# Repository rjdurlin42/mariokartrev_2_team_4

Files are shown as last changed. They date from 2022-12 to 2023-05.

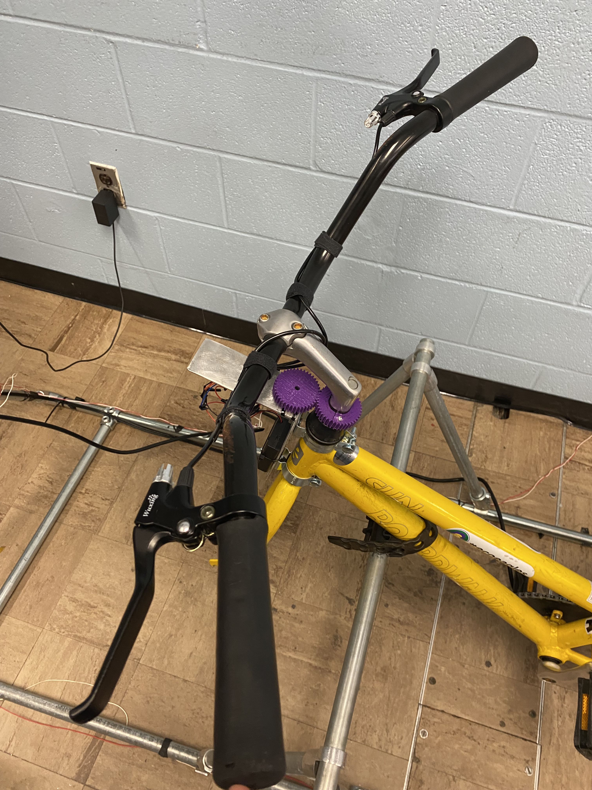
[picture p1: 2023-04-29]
Documentation/Images/Steering Sensor 2.jpg

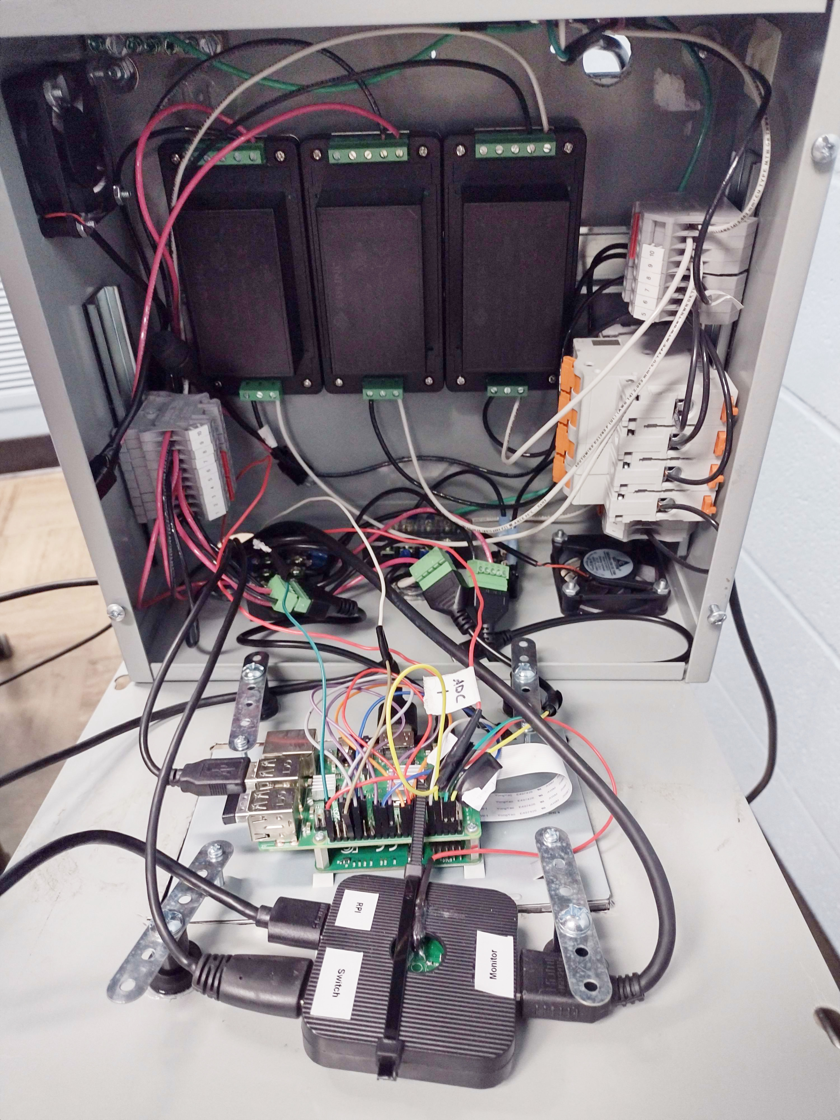
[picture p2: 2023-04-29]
Documentation/Images/Power Subsystem.jpg

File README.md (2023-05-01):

# Mario Kart Bike Version 2

## Executive Summary

The Capstone Design Project Team 4 collaborated to further enhance the riding experience offered by the existing Mario Kart Bike design. Team 4’s design adds a variable of resistance for two modes of operation: the Mario Kart Game Simulation and a Ride Replay Simulation (RRS).  

Improvements to the previous iteration of the Mario Kart Bike offer new dimensions of realism by adding a more dynamic resistance system, while the RRS enables users to record an actual bike ride and then replay it later indoors. Using data gathered from various sensors and an internal physics engine, the RRS processing subsystem calculates whether to speed up or slow down video playback based on the speed the user is pedaling, and it determines the appropriate resistance to apply.

The streamlined resistance system design replaced the cumbersome motor with a linear motor attached to an array of magnets, located perpendicular to a conductive flywheel to generate eddy currents. Opposing magnetic fields generate braking torque in the flywheel, which is transferred to the real bike wheel. This braking torque functions as the resistance felt by the user. The magnetic resistance system utilizes 85 states to create a smooth and realistic replay. The new resistance system also works in the original Mario Kart Bike Mode. 

Team 4 believes the Mario Kart Bike will have a significant impact on the general health of society when the commercialized version is used by Mario Kart enthusiasts and other gamers to participate in physical activity. We also believe our research to achieve a dynamic resistance system can be leveraged for other engineering applications.  

## Capabilities

The Dynamic Resistance System works as designed, providing resistance in the form of braking torque. At a minimum of 411 RPM of the flywheel, the maximum achievable braking torque is 19.432 Nm, and the minimum achievable braking torque is 0.097 Nm. At a maximum of 2,258 RPM of the flywheel, the maximum achievable braking torque is 38.865 Nm, and the minimum achievable braking torque is 0.972 Nm. The bike can be used to play Mario Kart levels, as well as dynamically apply resistance in the Mushroom Cup, via serial commands to the linear actuator. An HDMI switcher button and a play time popup were also implemented. Ride replay data gathering was a success. The Steering Sensor Subsystem is wireless and work as designed. The Speed Sensor Subsystem is hardwired and works as designed. The battery pack power supply for the Steering and Speed Sensor Subsystems is adequate for 2 weeks of run time while in constant use for 4 hours a day. Power distribution and protection comply with the design requirements. 

## Salient Outcomes

##### Dynamic Resistance System
- Resistance felt by the user is applied comparable an exercising spin bike
- Eddy currents are created by moving two magnets closer to a rotating aluminum disk
- Mode of operation: Mario Kart Gaming Simulation 
- Resistance system control
  - PID controller (Arduino Nano, PID_v1 library, maintains 25% duty cycle)
  - MOSFET H-Bridge with discrete components

##### Ride Replay Module (RRSA)
- Data collection (video, elevation, and speed)
- Data storage (removeable 128 GB SD card)
- Data processing (Raspberry Pi Zero W2 specified; Raspberry Pi B2 used due to supply shortage)
- Sensors 
  - Speed (utilizes a magnetic switch (reed switch) and a magnet mounted on bike wheel spoke)
  - Elevation (utilizes a pressure sensor)
- Automatic shutdown on low battery
- Battery life indicator LEDs on power supply

##### Steering and Speed Sensor Subsystems 
- Replaced Speed controller with an Arduino Nano 33 BLE to transfer data by Bluetooth communication
- Added Arduino Nano 33 BLE to the Steering Subsystem to enable the transfer of data by Bluetooth communication
- Designed system to power the Sensor Subsystems using battery packs with 4 lithium AA batteries
- MOSFET was added in the Speed Sensor circuit to save power

##### Steering Sensor Mount Enhancement
- Strengthened and stabilized steering sensor mount 
- Replaced existing plastic 3D printed L-Bracket with metal L-Bracket for enhanced strength
- Attached L-Bracket to bike with conduit hanger for stability 

##### Power Distribution
- Provides device and system protection
- Installation of over protection and Ground Fault Interruption (GFI) protection
- Complete replacement of 120 VAC power supply

## Project Demonstration & Images

Here is the link for the video showcasing the Mario Kart Bike being tested https://youtu.be/U-ZlnsXUXpw.





## About Us

### Team

Team 4 is a 5-person Capstone Design Project Team at Tennessee Technological University, who began Revision 2 of the Mario Kart Simulation Project during the Fall 2022 semester. Team members are Blake Pickett, Ray Durlin, Tyler Chittum, Benjamin Reed, and Sage Mooneyham. All members worked on the Resistance System.
<br />

samooneyha43
##### Sage Mooneyham
- Computer Engineering Major
- Software/Coding
- Bluetooth Communication
<br />

bcpickett42
##### Blake Pickett
- Electrical Engineering Major
- Hardware
- Sensor System
- Steering System
<br />

bdreed43
##### Benjamin Reed
- Computer Engineering Major
- Software/Coding
- HDMI Switching System
<br />

thchittum42
##### Tyler Chittum
- Electrical Engineering Major
- Hardware
- Ride Replay Simulation Acquisition (RRSA) System
<br />

rjdurlin42
##### Ray Durlin
- Electrical Engineering Major
- Hardware
- Power Distribution System

### Faculty Supervisor

The faculty advisor for this project is Jesse Roberts.

### Stakeholders

The main customer for this project is Jesse Roberts, however a commercialized version of this product would likely garner attention from people who enjoy playing Mario Kart, fitness, and/or cycling.

### Recognition

We would like to recognize the work of Reed Hester, Chase Griffin, and Leah Faulkner, the engineers who designed the first iteration of the Mario Kart Bike.

## Repo Organization

### [Reports](https://github.com/rjdurlin42/mariokartrev_2_team_4/tree/main/Reports)

Completed reports can be found in the Reports folder, or by clicking the link above.

### [Documentation](https://github.com/rjdurlin42/mariokartrev_2_team_4/tree/main/Documentation)

Project documentation can be found in the Reports folder, or by clicking the link above.

### [Software](https://github.com/rjdurlin42/mariokartrev_2_team_4/tree/main/Software)

Written software can be found in the Reports folder, or by clicking the link above.

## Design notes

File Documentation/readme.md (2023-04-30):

# Documentation

This folder holds documentation of the project, such as 3D models, wiring schematics, images, and approved signoffs.

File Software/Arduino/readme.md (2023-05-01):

# Arduino Code
This folder holds the code for the steering and speed sensors, as well as the RRS controller. This has both the serial and wireless method of communication with the speed sensor. For the RRS controller, no change is needed to the program for bluetooth as compared to wired serial. Dependencies are found in the include instruction at the top of each file. To run code on sensors, download the files in this folder, install Arduino IDE, install dependencies needed in Arduino IDE, and upload code to individual Nanos via USB. These files are used in conjunction with joycontrol, so you will want to run that as well.

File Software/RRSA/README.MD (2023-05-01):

This folder holds the script used to ride recording functionality in the RRSA subsystem, and the Testing folder contains scripts used to test the functionality of individual aspects of the RRSA. These scripts are designed to be run on the Raspberry Pi platform. In practical implementation, the /etc/rc.local file is configured to run the rrsa.py script on startup.

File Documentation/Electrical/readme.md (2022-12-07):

# Electrical

This folder holds wiring and general electrical schematics.

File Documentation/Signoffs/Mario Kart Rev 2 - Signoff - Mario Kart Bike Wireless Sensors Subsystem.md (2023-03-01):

# Mario Kart Rev 2 - Signoff - Mario Kart Bike Wireless Sensors Subsystem 
## Team 4 - Blake Pickett and Sage Mooneyham ##
<br/><br/>
### _Function of the Subsystem:_ ###

The function of the newly designed feature is to enable Bluetooth LE (BLE) connectivity between sensors and central Raspberry Pi (RPi). These sensors will gather, convert, and send data via BLE (achieved with usage of Arduino Nano 33 BLEs for each sensor) to the master RPi. The wires that rectify and step down the power for the sensors on the current version of the Mario Kart Bike will be replaced with 4 AA batteries and a holder. The 4 AA batteries will provide 6 V and 3500 mAh to the microcontrollers, which will power the sensors for more than 2 weeks.    
<br/><br/>

### _Constraints:_ ###

* **Run Time:**
  * Batteries must supply the DC voltage and current needed to power the equipment for 2 weeks. The equipment shall be able to with stand a minimum of 4 hours of constant use each day during the 2 weeks.     

* **Speed Sensor:** 
  * The KY-032 Obstacle Avoidance Sensor (tachometer) must have a DC voltage between 3.3 V and 5 V, and a minimum of 20 mA to operate correctly. [1]
  * The MIC94053 P-Channel MOSFET must have an input voltage from 1.8 V to 5.5 V. [2] 
  * The MIC94053 P-Channel MOSFET must allow a drain current of 20 mA.  
  * The Nano 33 BLE must have a DC voltage between 5 V and 21 V. [3]
  * The current through the 3.3 pin on the Nano 33 BLE must be less than 100 mA. [4]     

* **Steering Sensor:** 
  * The Potentiometer voltage must be the same as the analog to digital converter (ADS1015).    
  * The ADS1015 must have a DC voltage between 0 V and 5.5 V. [5] 
  * The Nano 33 BLE must have a DC voltage between 5 V and 21 V. [3]
  * The current through the GPIO pins on the Nano 33 BLE must be less than 15 mA. [3]

* **Data Transfer Method:**
  * Communication between the sensors and main RPi must be wireless. Each sensor must have a corresponding Nano 33 BLE in order to achieve BLE communication.

* **Latency:**
  * Communication latency from data sensors to central microcontroller shall be at maximum 40 ms.

<br/><br/>
### _Buildable Schematic:_  ###   

The wiring schematics for the speed and steering sensors are provided in **Figures 1** and **2**.  



**Figure 1.** Wiring Schematic for the Speed Sensor
<br/><br/>



**Figure 2.** Wiring Schematic for the Steering Sensor

<br/><br/>
### _Analysis:_ ### 
<br/><br/>

* **Power Supply for the Speed Sensor:** 
<br/><br/>

  * **_Speed Sensor Batteries:_**
  
      * AA Battery Current = 3500 mAh [6]
      * AA Battery Voltage = 1.5 V [6]
      * Total AA Batteries Voltage = 1.5 * 4 = 6 V
      * Total AA Batteries Wattage = 6 * 3500 = 21000 mWh

  * **_Speed Sensor Current:_**
    
      * Tachometer (running) = 20 mA [1]
      * Tachometer (sleeping)  = 0 mA 
         * The MOSFET is in the cut-off region when Vgs > - Vth. The Vgs = 3.3 – 3.3 = 0  V. The Vth minimum value is - 0.5 V and the maximum value is -1.2 V [2]. Since Vgs = 0 V > Vth = -0.5 V, the drain current Id = 0 A. The tachometer sleeping current is equal to the drain current. 
      * MIC94053 P-Channel MOSFET Current = 0.005 mA [2] 
      * Arduino Nano 33 BLE Default Run Settings = 17 mA [7]  
      * Arduino Nano 33 BLE Sleep Mode (Ram Retention, wake on RTC event) = 0.00316 mA [8]
    <br/><br/>
         * Max current going through 3.3 pin  =  20 mA
         * Current needed (running) = 20 + 17 + 0.005 = 37.005 mA
         * Current needed (Sleeping) = 0 + 0.00316 + 0.005 = 0.00816  mA
         * Total Amp-Hours Needed = (37.005 * 56) + (0.00816  * 280) = 2074.56 mAh    
        
    The speed sensor will use 2075 mAh in 2 weeks of use, which is less than the 3500 mAh that the battery can supply. 
    
    The max current going through the 3.3 pin is 20 mA which is less than 100 mA that the 3.3 pin can with stand. 
    
    The tachometer will be supplied 20 mA when running and 0 mA when sleeping. 
    
    The MIC94053 P-Channel MOSFET will allow a drain current of 20 mA through the MOSFET because the drain current is less than 1.4 amps [2]. The tolerance for the drain current is 1.4 amps [2].
<br/><br/>

  * **_Speed Sensor Voltage:_**
<br/><br/>
    

    **Figure 3.** Discharge of the Ultimate Lithium Energizer AA Battery [6]

    From **Figure 3**, the voltage from of a battery discharging 10 mA or 100 mA drops from 1.5 V to 1.3 V. 

     * Total Voltage Before Discharging =  1.5 * 4 = 6 V 
     * Total Voltage After Discharging =  1.3 * 4 = 5.2 V 

    Therefore, the voltage will stay above the 5 V cutoff voltage of the Arduino Nano 33 BLE even when the batteries have dissipated the full 3500 mAh.

    The input voltage will be regulated by the voltage regulator on the Arduino Nano 33 BLE to 3.3 V. 
    
    The tachometer will be supplied 3.3 V when running and 0 V when sleeping. 
    
    The MIC94053 P-Channel MOSFET will receive 3.3 V for the input voltage which is between 1.8 V and 5.5 V. 
    <br/><br/>

  * **_Speed Sensor Power:_**

    * Tachometer (running) = 20 * 3.3 = 66 mW
    * Tachometer (sleeping) = 0 V * 0 A = 0 mW
    * MIC94053 P-Channel MOSFET Power Dissipation = (Id )^2 * Rds = (20*10^-3)^2 * 76 * 10 ^-3 = 0.0304 mW  
       * Id = tachometer (running) = 20 mA
       * Rds = 76 m ohms [2]
    * Arduino Nano 33 BLE Default Settings = 17 * 6 = 102 mW 
    * Arduino Nano 33 BLE Sleep Mode (Ram Retention, wake on RTC event) = 0.00316* 6 = 0.01896 mW
    <br/><br/>
       - Watts needed (running) = 66 + 102 + 0.0304 = 168.0304 mW  
       - Watts needed (sleeping) =  0 + 0.01896 + 0.0304 = 0.4936 mW
       - Total Watt-Hours Needed = (168.0304  * 56) + (0.4936  * 280) = 9423.5232 mWh  

    The speed sensor will use 9424 mWh in 2 weeks of use. Four AA batteries will provide 21000 mWh, which is sufficient to run the speed sensor equipment for 2 weeks including the 4 hours of constant use each day.
    <br/><br/>

  * **_Speed Sensor Run Time:_**

    Power can be preserved by turning on and off the tachometer (GPIO Pin 22 will be connected to the gate of the MIC94053 P-Channel MOSFET), power LED, and I2C pull-up resistors when needed (done in software) [9][10]. 
    
    A low signal will be asserted to Pin 22 to turn on the tachometer. This will complete voltage connection from the Nano voltage pin (pin 2) to the Tachometer voltage pin( Vcc) allowing current to flow through the tachometer.
    
    A high signal will be asserted to Pin 22 to turn off the tachometer. This will break the voltage connection from the Nano voltage pin (pin 2) to the Tachometer voltage pin( Vcc), creating an open circuit, allowing no current to flow through the tachometer.
    
    This Nano is awoken by event using the RTC timer on the nRF52840 processor. Every 10 seconds (this number is chosen so as to connect in a timely fashion if user wants to activate the controller, while still keeping Nano in sleep a majority of the time), the Nano used for speed data communication will check to see if the central RPi is looking for connection (this means user is attempting to use device). If so, Tachometer is turned back on and actions made before sleeping are reverted. If central RPi is not broadcasting for connection, the Nano will reenter sleep mode (RTC counter).
    
    Dimensions of the battery holders are 2.248 inches (L) by 2.457 inches (w) by 0.622 inches (h). The holders are small/compact to avoid the trip hazard posed by the long wires. Zip ties will securely mount the battery holder to the bike frame. 
    <br/><br/>
    <br/><br/>
    
* **Power Supply for the Steering Sensor:**
    <br/><br/>
    * **_Steering Sensor Batteries:_**

      * AA Battery Current = 3500 mAh [6]
      * AA Battery Voltage = 1.5 V [6]
      * Total AA Batteries Voltage = 1.5 * 4 = 6 V
      * Total AA Batteries Wattage = 6 * 3500 = 21000 mWh

    * **_Steering Sensor Current:_**
    
      * Potentiometer  (running) = 10k ohms [11] = 3.3/10000 = 0.33 mA
      * Potentiometer (sleeping) = 0 / 10000 = 0 mA
      * ADS1015 = 0.3 / 3.3 = 0.09091 mA 
      * Arduino Nano 33 BLE Default Settings = 17 mA [7]    
      * Arduino Nano 33 BLE Sleep Mode (Ram Retention, wake on GPIOTE event) = 0.01737 mA [8]
        <br/><br/>
         - Max current going through IO pins = 0.33 mA
         - Current needed (running) = 0.33 + 0.09091 + 17 = 17.421 mA
         - Current needed (sleeping) = 0 + 0.09091+ 0.01737 = 0.10828 mA
         - Total Amp-Hours Needed = (17.421 * 56) + (0.10828 * 280) = 1981.47 mAh 

      The steering sensor will use 1982 mAh in 2 weeks of use, which is less than the 3500 mAh that the battery can supply.  
      
      The max current going through the GPIO pins is 0.33 mA which is less than 15 mA that the GPIO pins can with stand. 
      <br/><br/>

    * **_Steering Sensor Voltage:_**
    
      From **Figure 3**, the voltage from of a battery discharging 10 mA or 100 mA drops from 1.5 V to 1.3 V.  

         * Total Voltage Before Discharging =  1.5 * 4 = 6 V 
         * Total Voltage After Discharging =  1.3 * 4 = 5.2 V 

      Therefore, the voltage will stay above the 5 V cutoff voltage of the Arduino Nano 33 BLE even when the batteries have dissipated the full 3500 mAh. 

      The input voltage will be regulated by the voltage regulator on the Arduino Nano 33 BLE to 3.3 V.
      
      The GPIO pins will output 3.3 V when given a high signal and 0 V when given a low signal.
      
      The potentiometer and the ADS1015 will be supplied with 3.3 V when their IO pins are given a high signal. Therefore, the voltage on the potentiometer and the ADS1015 will be the same. 
      <br/><br/>

    * **_Steering Sensor Power:_**

        * Potentiometer (running)= 0.33 * 3.3 = 1.089 mW
        * Potentiometer (sleeping) = 0 A * 0 V = 0 mW
        * ADS1015 = 0.3 mW [5]
        * Arduino Nano 33 BLE Default Settings = 17 * 6 = 102 mW 
        * Arduino Nano 33 BLE Sleep Mode (Ram Retention, wake on GPIOTE event) = 0.01737 * 5 = 0.10422 mW
        <br/><br/>
            - Watts needed (running) =  1.089 + 0.3 + 102 = 103.389 mW
            - Watts needed (sleeping) = 0 + 0.3 + 0.10422 = 0.40422 mW
            - Total Watt-Hours Needed = (103.389 * 56) + (0.40422 * 280) = 5902.97 mWh

        The speed sensor will use 5903 mWh in 2 weeks of use. Four AA batteries will provide 21000 mWh, which is sufficient to run the speed sensor equipment for 2 weeks including the 4 hours of constant use each day.
        <br/><br/>

    * **Steering Sensor Run Time:**

      Power can be preserved by turning on and off the potentiometer (Nano GPIO Pin 20), power LED, and I2C pull-up resistors when needed (done in software)[9][10]. 
      
      A high signal will be asserted to pin 20 to turn on the potentiometer. 
      
      A low signal will be asserted to pin 20 to turn on the potentiometer. 
      
      The Arduino Nano 33 BLE will go into sleep mode after the potentiometer, power LED, and I2C pull-up resistors are turned off. Before sleeping, Nano will use the endTransmission Arduino function to end I2C communication. 
      
      The Nano can be woken via a GPIO interrupt event. The GPIO interrupt event that will awaken the switch will be on pin 25 as well as 26 (left and right handlebar button). When the user presses either/both of these, the Nano will wake from sleep, and connect to the central RPi, as well as revert previous actions before it slept.

      Dimensions of the battery holders are 2.248 inches (L) by 2.457 inches (w) by 0.622 inches (h). The holders are small/compact to avoid the trip hazard posed by the long wires. Zip ties will securely mount the battery holder to the bike frame.
      <br/><br/>

 * **Strobing of Receiver:** 

    IR light is emitted from the KY-032 at a frequency of 38 kHz [12], so the receiver (HS0038B) must be cycling at 76 kHz (as a minimum) to satisfy the Nyquist sampling rate. This strobe rate can be programmed manually.  The KY-032 sensor will use the enable pin, which should not be active for more than 2 ms at a time due to the receiver quickly saturating when active [12].

    By determining the time between any two high readings (two markings) and multiplying this time by the number of individual markings, the time required to perform each revolution of the flywheel can be calculated (this calculation will update between every 2 high readings).    

      - (Time between two highs) * (Number of markings) = Time for 1 revolution

    By using the gearing ratio between the flywheel and the bike tire, the current revolutions per second (or minute) at the bike tire can be calculated.    
    <br/><br/>

 * **Bluetooth Connectivity:**

    BLE connectivity for the steering sensor’s microcontroller can use the sensor in conjunction with the ADS 1015 and Potentiometer as well as the left and right handlebar buttons on the bike.    

    Arduino microcontrollers surpass the 5 V limit while others are at 5 V exactly. The Arduino Nano 33 BLE satisfies the power constraint. The Nano 33 BLE measures 45 mm by 18 mm and will within the space constraints of the Mario Kart Bike’s long metal pipes.     
    <br/><br/>

 * **Latency:**

    Latency of communication shall be 40 ms. Network latency can be calculated with the following formula [13]:

      - Latency=(d/v)+(s/r)

    where:

    d = distance of communication in m

    v = speed of transmission medium in m/s

    s = packet size in bits

    r = data transmission rate in Kbps

    In the worst case, the distance equals 2.44 m (central RPi to speed sensor). The transmission speed of Bluetooth LE is 3 * 10^8 m/s (radio waves through air). The maximum transfer unit (MTU) of BLE is 184 bits. Finally, the data transmission rate of the Nano 33 BLE is 270 Kbps. This gives a max transmission latency of 0.68 ms.
    <br/><br/>

 * **Coding:**

    Coding of the Bluetooth modules and their respective microcontrollers can be accomplished in the Arduino IDE, which supports the programming languages C++ and C.  

    Designation of microcontrollers is important, with the sensor’s microcontrollers being peripheral, strictly sending data.  

    The RPi housed in the main component box will be the central microcontroller, or master, primarily receiving data from the peripheral microcontrollers and potentially controlling them if necessary.
    <br/><br/>

  * **Profiles:**

    Bluetooth LE uses a concept of profiles as specification for Bluetooth communication by creating rules that allow certain tasks to be accomplished. The sensors will send bit data to a central RPi, so the Serial Port Profile (SPP) will be used. This profile will define how to set up virtual serial ports and connect two Bluetooth LE enabled devices. 

<br/><br/>
### _BOM:_ ### 

The bill of materials (BOM) to accomplish the design illustrated in the schematics is provided in **Table 1**. 

**Table 1.** Bill of Materials
| Brand / Manufacturer | Part Name | Supplier | Part / Model # or ASIN # | Qty | Units  | Unit Cost | Cost |
| --- | --- | --- | --- | --- | --- | --- | --- |
| LAMPVPATH | 4 AA Battery Holders | Amazon | B07L9M6VZK | 1 | Pack | $7.49 | $7.49  |
| Energizer | 24 Pack AA Lithium Batteries | Amazon | B07BMH7RDP | 1 | Pack | $65.35 | $65.35 |
| Microchip Technology | MIC94053YC6-TR | Digi-key | MIC94053YC6-TR | 1 | Piece  | $0.74 | $0.74  |
| HMROPE | 8 Inch Zip Ties | Amazon | TXLAC | 1 | Pack | $9.18 | $9.18  |
| Duck | Electrical Tape | Amazon | 282289 | 1 | Roll | $1.48 | $1.48  |
| Arduino | Nano 33 BLE | Arduino  | ABX00030 | 2 | Pieces | $26.30 | $52.60 |

<br/><br/>
**References** 

[1]	ArduinoModules, Olawale, I., Ryerson, B., & Chavan, S. (2023, February 15). KY-032 infrared obstacle avoidance sensor module. ArduinoModulesInfo. Retrieved February 24, 2023, from https://arduinomodules.info/ky-032-infrared-obstacle-avoidance-sensor-module/ 

[2] 84mΩ p-channel MOSFET in SC-70-6 - Microchip Technology. (n.d.). Retrieved March 1, 2023, from https://ww1.microchip.com/downloads/en/DeviceDoc/mic94052-53.pdf 

[3] Store.arduino.cc/Nano-33-BLE. (n.d.). Retrieved March 1, 2023, from https://docs.arduino.cc/static/0877c2bf863b3473e961b0b72c8e68ec/ABX00030-full-pinout.pdf 

[4] How to power your arduino? Vin, 5V, and 3.3V pins. How to Power Your Arduino? Vin, 5V, and 3.3V Pins. - Circuit Journal. (n.d.). Retrieved March 1, 2023, from https://circuitjournal.com/arduino-power-pins#:~:text=3.3V%20Pin%20as%20a%20Power%20Output.%20You%20can,can%20supply%20about%20100%20to%20150mA%20of%20current. 

[5] ADS1015. ADS1015 data sheet, product information and support | TI.com. (n.d.). Retrieved March 1, 2023, from https://www.ti.com/product/ADS1015 

[6]	Energizer L91 specifications ultimate lithium. (n.d.). Retrieved February 24, 2023, from https://data.energizer.com/pdfs/l91.pdf 

[7] Team, T. A. (n.d.). Arduino docs: Arduino Documentation. Arduino Docs | Arduino Documentation. Retrieved February 13, 2023, from https://docs.arduino.cc/ 

[8] Arduino. (n.d.). Retrieved February 21, 2023, from https://content.arduino.cc/assets/Nano_BLE_MCU-nRF52840_PS_v1.1.pdf

[9]	How to reduce power consumption on the nano 33 ble. (n.d.). Retrieved February 21, 2023, from https://support.arduino.cc/hc/en-us/articles/4402394378770-How-to-reduce-power-consumption-on-the-Nano-33-BLE 

[10]	Arduino® Nano 33 ble. (n.d.). Retrieved February 21, 2023, from https://docs.arduino.cc/resources/datasheets/ABX00030-datasheet.pdf

[11] Industries, A. (n.d.). Stemma wired potentiometer breakout board - 10K ohm linear. adafruit industries blog RSS. Retrieved March 1, 2023, from https://www.adafruit.com/product/4493#description 

[12]	IR sensor for obstacle avoidance KY-032 (AD-032). IR Senor Obstacle Avoidance Keyes KY 032. (n.d.). Retrieved February 5, 2023, from http://irsensor.wizecode.com/

[13] RF Wireless World. Network Latency Calculator | Network Latency Formula. (n.d.). Retrieved February 13, 2023, from https://www.rfwireless-world.com/calculators/Network-Latency-Calculator.html

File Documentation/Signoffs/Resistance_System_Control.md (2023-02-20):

Team 4 – Mario Kart & Ride Replay Simulator

Team Members: Ray Durlin, Blake Pickett, Tyler Chittum, Benjamin Reed, and Sage Mooneyham

## Detail Design: Resistance System Control Circuit ##

Please note: the scope of this signoff extends only to the control cicuit itself, not to housing components, to the linear actuator, nor to connectors. Also, the signoff document for the resistance system contains BOM listings and information redundant to this document.

### Function of the Subsystem:

- This subsytem acts to control the linear actuator used in the ride resistance system.
- Controls both the direction and speed of the linear actuator.
- Takes an input from the ride replay subsystem over a wireless connection, which determines the distance set point for the linear actuator.
- Takes an input from the linear actuator feedback to determine the current position of the actuator.

### Constraints:

#### Actuator Duty Cycle

The duty cycle of the utilized linear actuator is 25 %. This value must not be exeeded during normal operation. As a result, the controller must be programmable so that the duty cycle may be limited.

#### Actuator Driving Voltage

The utilized actuator is rated for operation at 12 VDC. The control circuit must be capable of providing this voltage to the actuator during operation, so the absolute value of the voltage across the actuator while the system is in either of the two possible on states (foreward and reverse) shall be constrained to 12 V +/- 1 %, assuming the power subsystem provides an input voltage regulated to 12 VDC.

#### Current Capability

The utilized actuator draws a stall current of 7 A, and has a nominal current draw from 1.1 A to 3.4 A. The control circuit must be capable of handling a motor stall without undergoing thermal overload. In addition, the utilized power connector must be capable of handling the total current demand.

#### Wireless Communications

The control ciruit must be capable of recieving a wirelessly-transmitted digital signal from the ride replay system using Bluetooth to update the actuator's position. Since human reaction time is limited to between 100 and 200 ms [1], it follows that the period of data transmission for each packet containing a position value be constrained to be less than 100 ms.

#### Back-EMF Protection

In the course of operation, particularly when the motor is switched off suddenly, a transient voltage potential known as back-EMF will be generated by the motor with opposite polarity to its driving voltage. Due to this, the control circuit shall contain freewheeling diodes to shunt the resulting current away from the switching transistors to prevent damage to the transistors.

#### Mountability

The PCB layout must account for the need to mount the circuit within its housing, as such, screw holes shall be included in the PCB design.

#### Stability

The device must operate without becoming unstable.

#### Resolution

The resistance system has been specified to provide at least 85 unique resistance states, or lengths of linear actuator extension when operating within the specified wheel speed range (from 116 RPM to 288 RPM). To this end, the controller must be capable of monitoring and responding to even the smallest changes in actuator extension correpsponding to a change in resistance state. Please note: from manufacterer correspondance, it is known that it is impossible to guarantee the repeatability of the linear actuator for any controller; furthermore, the actuator to be controlled has already been approved for use. As such, it is impossible to assess the ability of this subsystem to acheive the desired precision from this linear actuator or to select a different linear actuator.

### Schematic and PCB Layout

Schematic

Figure 1: a schematic for the control circuit.

pcb

Figure 2: the PCB layout for the design.

The design files are included within the Electrical subdirectory of the Documentation directory. See links: [schematic](https://github.com/rjdurlin42/mariokartrev_2_team_4/blob/main/Documentation/Electrical/Ride%20Resistance%20System%20Control%20Circuit.png), [pcb](https://github.com/rjdurlin42/mariokartrev_2_team_4/tree/main/Documentation/Electrical/PCB/Sources/Ride%20Resistance%20System%20Control%20Circuit).

### Analysis

#### Actuator Duty Cycle

Arduino PID library contains a function to limit the minimum and maximum PWM duty cycle [2].

Function usage:

     SetOutputLimits(min, max)
     min: the minimum PWM duty cycle
     max: the maximum PWM duty cycle

Where min and max are 8-bit integers, and may be directly-addressed.

The Arduino Nano sets the PWM duty cycle so the maximum PWM cycle may be programatically limited to satisfy the constraint as follows:

     SetOutputLimits(0, 63); //63 is floor[(255)*(25 %)]

Therefore, the constraint is satisfied.

#### Actuator Driving Voltage

     Full load actuator current = 3.4 A @ 12 V
     Linear approximation for motor resistance: Rmotor = 3.529 Ω
     Rds_on(Q1,Q2) = 18 mΩ = 0.018 Ω
     Rds_on(Q3,Q4) = 4.4 mΩ = 0.0044 Ω
     Minimum actuator voltage satisfying constraint = 12 V - 12*0.01 V = 11.88 V

Circuit Analysis:

     On state 1 [Q1 and Q4 on, Q2 and Q3 off]
          |Actuator voltage| = (12 V)*(3.529 Ω)/(3.529 Ω + 0.018 Ω + 0.0044 Ω) = 11.92 V < 11.88 V
     
     On state 2 [Q1 and Q4 off, Q2 and Q3 on]
          |Actuator voltage| = 11.92 V < 11.88 V [by symmetry]

Constraint met.

#### Current Capability

     Linear actuator current at stall = 7 A
     Nominal linear actuator voltage = 12 V
     AMASS XT30 connector current rating = 15 A
     Imax_continuous(Q1,Q2) = 24 A
     Imax_continuous(Q3,Q4) = 45 A
     Stall (worst-case) resistance = (12 V)/(7 A) = 1.714 Ω

By simulation:

     Pd(Q1,Q2) = 1.05 W  < 78 W  = Pmax(Q1,Q2)
     Pd(Q3,Q4) = 0.601 W < 2.5 W = Pmax(Q3,Q4)

Constraint met.

PWM Control Simulation Details:

    Duty Cycle = 25 %
    Switching Frequency = 24 kHz
    Motor Stalled
    Polarity (directional) change at 300 ms
    Switching delay time: 208 to 300 ms
    
spicesim
Figure 3: the LTSPICE schematic prepared for this SPICE simulation.

loadcurrent
Figure 4: the load current. The polarity reverses as expected during the simulation of the directional change starting at 300 microseconds. During the high portions of the PWM cycle, the load current is close to the ideal value of 7 A, meaning the H-bridge produces minimal voltage drop.

Note: It is impossible to fully simulate a motor in SPICE without knowing several mechanical characteristics (moment of inertia, coefficient of viscous friction, and torque) [3] and this information is not given by the actuator manufacturer, so a worst-case non-reactive approximation was used. Back-emf simulation impossible for this reason.

#### Wireless Communications

    Ts < 100 ms = 0.1 s
    Distance resolution: 10 bits (limited by microcontroller ADC)
    Communication protocol: serial
    Communication frequency > 1/(0.1 s) = 10 Hz
    Required samples to update distance variable = (10 bits)/(1 bit/sample) = 10 samples
    Required baud rate > (10 Hz)*(10 samples) = 100 Baud < 9600 = HC-06 default baud rate

Contstraint met.

#### Back-EMF Protection

    Vf(D1,D2,D3,D4) = 0.5 V (approximately)
    Vf(Q1,Q2,Q3,Q4) = 1 V (approximately)
    Rated Peak Current(D1,D2,D3,D4) = 100 A

Specified in datasheet for free-wheeling applications such as this; constraint met.

#### Mountability

Four 2.5 mm diameter screw holes have been included in the PCB design (see fig. 2). These screw holes can accommodate #3 screws. Mounting and housing cutouts to be detailed in motor stand signoff.

#### Stability

Arduino programmable as PID controller [4].

Manufacturer-provided PID constants [5]:

    Kp = 1.80
    Ki = 0.0900
    Kd = 2.50

The above can reasonably be assumed to produce a stable system; therefore, constraint met.

#### Resolution

    Full actuator range = 50.04 mm

Please note: the above value is **not the usable range**, but the full range of the actuator itself; it is stated to clarify the analysis which follows.

    Tmax(max speed) = 121.8499 N•m
    Tmin(max speed) = 0.2712 N•m
    Tmax(min speed) = 28.901 N•m
    Tmin(max speed) = 0.0643 N•m
    See tables 1 and 2 in the resistance system signoff for full specified torque ranges
    Precision of controller: 16 bits
    Unique ADC states across full range = 2^16 = 65536
    ADC full scale range: 0 to 6.144 V
    Feedback voltage range: 0 to 5 V
    ADC States across feedback voltage range: floor[65536*(5 V)/(6.144 V) = 53333]
    Distance precision = (50.04 mm)/(65536) = 0.9382 μm

Using a spreadsheet: (see [Controller_Analysis.xlsx](https://github.com/rjdurlin42/mariokartrev_2_team_4/blob/main/Software/Controller_Analysis.xlsx)):

Equation used:

d_equation

    d:  distance of magnet from flywheel (corresponding to actuator extension lengths)
    Td: developed torque
    ρ:  conductivity
    D:  diameter of magnet
    t:  flywheel thickness
    u0: magnetic permiability of free space
    m:  magnetic dipole moment
    R:  radius of flywheel
    w:  flywheel angular velocity
    Evaluation method: compare the actuation distance required to increment a state at the extrema of the specified 85-state sequences for minimum and maximum speed; compare to determine the smallest distance required to increment a state.
    Result: 10.9 μm
    See EXEL workbook for constant values and formulae
    0.9382 μm < 10.9 μm

Constraint met.

Table 1: miscellaneous component notes and design considerations.
| Component(s) | Design Considerations |
|---|---|
| Switching Transistors (Q1, Q2, Q3, Q4) | Q1 and Q2 only need to switch when the actuator changes direction, and a delay can be programmatically implemented to ensure no current flows during the switching of these transistors. Q3 and Q4 must be able to switch fast enough to handle Pulse Width Modulation (PWM). These FETs have rise and fall times on the order of tens of nanoseconds. As such, they should be capable of handling a PWM signal in the kHz range. |
| Back-EMF Protection Diodes (D1, D2, D3, D4) | Compared to the body diodes of the utilized transistors (Vf ~ 1 V), these diodes provide a forward voltage of equal to or less than 0.5 V, effectively bypassing the transistors during reverse-conduction. |
| Resistors (All) | All resistors in this circuit were subject to only very small power dissipations: less than a milliwatt in all cases. As such, small, common ¼ W resistors were selected. Gate resistors were selected to be surface mount chip-resistors to minimize space usage. The gate driver resistors for the P-Ch FETs are larger than those for the N-Ch FETs, as switching speed is not a priority for the P-Ch FETs. The PWM will be done on the N-Ch FETs, and it is vital that the voltage drop across the gate driver IC be minimized to ensure complete biasing at steady-state.  |
| Pre-Biased Dual NPN IC (U1) | This component is used to bias the gates of the P-Ch FETs, as turning these transistors off will require a voltage of 12 V – a voltage not achievable by using the microcontroller alone. This component was selected because it combines the utility of four resistors and two BJTs into a single package. |
| Arduino Nano (A1) | This microcontroller module was selected because it is already in our stock. It provides an on-board voltage regulator capable of regulating to 3.3 V and to 5 V. The 5 V supply is ideal for providing a logic-voltage reference to the linear actuator feedback and powering the HC-06 module. This microcontroller has a 10-bit DAC on board. |
| Bluetooth Module (MD1) | The HC06 should be capable of providing the required range, as it has a maximum range of about 10 m. In addition to being inexpensive, this module also has the benefit of being very easily connected; it requires only four pins to be connected to the external circuit. |
| Power Connector | The component handles the power input to the circuit, which is then fed into the linear actuator. As such, it must be rated to handle slightly over 7 amperes of current. The AMASS XT30 is rated for 15 A. It also does not allow the user to connect the polarity incorrectly and the mating connector is commonly available in a form that lends itself to the easy fabrication of cables of a custom length without any special equipment. |

### Bill of Materials

Table 2: a BOM for the design. Please note that the Arduino Nano is already in our inventory.

| Level | Part # | Part Name | Supplier |  Supplier Part # | Qty |  Units | Unit Cost | Cost  |
| --- | --- | --- | --- | ---| --- | --- | --- | --- |
| 1 | HBRIDGE100 | Assembly | None | None |  1  |  Assy  | | |
| 1.1 | SOCK100 | AMASS XT30 DC Connector - Male | TME | XT30PW-M |  1  |  Piece | $0.63 |  $0.63  |
| 1.2 | MOSFET100 | G26P04K P-Channel MOSFET | DIGIKEY | 3141-G26P04KCT-ND |  2  |  Piece | $0.78 |  $1.56  |
| 1.3 | MOSFET101 | AOD424 N-Channel MOSFET | DIGIKEY | 785-1565-1-ND |  2  |  Piece | $0.98 |  $1.96  |
| 1.4 | WIFIREC100 | HC-06 Bluetooth Transceiver | ALIEXPRESS  | HC-06 |  1  |  Piece | $2.24 |  $2.24  |
| 1.5 | SOCK200 | Socket Header for Transceiver | DIGIKEY | 2057-SMC-1-04-1-GT-ND  |  1  |  Piece | $0.33 |  $0.33  |
| 1.6 | DIODE100 | B320 Schottky Diode | DIGIKEY | B320-FDICT-ND |  4  |  Piece | $0.48 |  $1.92  |
| 1.7 | BJT100 | DDC114YU-7-F Dual Pre-biased BJT (NPN) | DIGIKEY | DDC114YU-FDICT-ND |  1  |  Piece | $0.43 |  $0.43  |
| 1.8 | CHRESIST100 | CRCW120610K0JNEA 10k Chip Resistor | DIGIKEY | 541-10KECT-ND |  2  |  Piece | $0.10 |  $0.20  |
| 1.9 | CHRESIST101 | ERJ-8GEYJ102V 1k Chip Resistor | DIGIKEY | P1.0KECT-ND |  2  |  Piece | $0.14 |  $0.28  |
| 1.10 |  CARBRESIST100  | CFR-25JB-52-1K 1k THT Resistor | DIGIKEY | 1.0KQBK-ND |  3  |  Piece | $0.10 |  $0.30  |
| 1.11 |  CARBRESIST101  | CFR-25JB-52-2K2 2.2k THT Resistor | DIGIKEY | 	  2.2KQBK-ND |  1  |  Piece | $0.10 |  $0.10  |
| 1.12 | ARDNANO100 | Arduino Nano Microcontroller | Arduino | A000005 |  1  |  Piece | $24.90  |  $24.90 |
| 1.13 | SOCK300 | Socket Header for Arduino | DIGIKEY | 2553-2042-1X15G00SA-ND |  2  |  Piece | $0.74 |  $1.48  |
| 1.14 | ADC100 | ADS1115 4-Channel 16-Bit ADC Module | Protosupplies | MOD-83 |  1  |  Board | $5.95 |  $5.95  |
| 1.15 | SOCK400 | Socket Header for ADC Modele | DIGIKEY | 	ED5864-10-ND |  1  |  Piece | $2.52 |  $2.52  |
| | | | | | | | Total |  $44.80 |

### Citations

[1]R. Whelan, “Effective analysis of Reaction Time Data,” The Psychological Record, vol. 58, no. 3, pp. 475–482, 2008.

[2]B. Beauregard, "SetOutputLimits()," Arduino Playground. [Online]. Available: https://playground.arduino.cc/Code/PIDLibrarySetOutputLimits/. [Accessed: 10-Feb-2023]

[3]"Using SPICE To Model DC Motors," Precision Microdrives. [Online]. Available: https://www.precisionmicrodrives.com/ab-025. [Accessed: 04-Feb-2023].

[4]B. Beauregard, "Arduino PID Library," Arduino Playground. [Online]. Available: https://playground.arduino.cc/Code/PIDLibrary/. [Accessed: 08-Dec-2022]. 

[5]"Pololu - Glideforce GF23-120502-3-65 high-speed LD linear actuator with feedback: 12kgf, 2’ stroke (1.97’ usable), 3.3’/s, 12V," Pololu Robotics &amp; Electronics. [Online]. Available: https://www.pololu.com/product/4951. [Accessed: 08-Dec-2022].

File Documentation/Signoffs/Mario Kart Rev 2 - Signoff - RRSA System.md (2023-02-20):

# Mario Kart Rev 2 - Signoff - Mario Kart Bike RRSA
## Team 4 - Tyler Chittum ##

### Function

The function of the ride data acquisition system is to collect the data necessary to replay rides taken by a rider. The system is required to collect the following: speed, altitude, and video footage. The system records this data and transfers it to the ride replay system by Bluetooth when in proximity.

### Constraints

**C1. Sensor Constraints:** 

The combined inaccuracy of the pressure sensor, the speed sensor, and the resistance system is to be below 10 %.

**C1.1. Pressure Sensor:** The required precision to achieve +/- 1 % accuracy at a granularity of 1 kCal is +/- 4.67 cm. The ride data is to be digitally filtered to attenuate out any ride noise above 1 Hz, so altitude data must be sampled at at least 2 Hz [Nyquist theorem].

**C1.2 Speed Sensor:** The bike wheel speed must be sampled at a frequency of at least 9.6 Hz as the maximum specified bike wheel rotational frequency is 288 RPM, or 4.8 Hz [Nyquist theorem].

**C2. Video Recording:** 

**C2.1. Video Quality:** The resolution is to be 720p with a frame rate of at least 30 fps, and the camera is to be compatible with the Raspberry Pi Zero 2W's camera serial interface. 

**C2.2. Video Data Syncing:** The video footage recorded is to be in sync with the data being measured by sensors.

**C3. Battery life:** The device must be able to continuously operate for at least 3 hours and must provide the user with a visual indication of battery charge status.

**C4. Recording capacity:** The device must be able to capture 3 hours of continuous footage and measurements. 

**C5. Usability:** The device must provide an easily used interface, which is also unobtrusive and does not distract the rider.

**C6. Durability:** The device is to be protected from the outside environment with all electrical components secured to prevent damage while the user is riding.

**C.7 Device Fitment:** The device is to be capable of mounting on any standard mountain bike with no obstructions to the video recording.

### Schematic:

RRSA Schematic
Figure 1: a schematic for the assembly. Not pictured: the camera, which is to be attached to the camera port on the Raspberry Pi Zero 2W.

Overhead View
Figure 2: a drawing illustrating the placement of modules within the project box. The mounting plate is covered in 2.54 mm width square holes. The battery is to be affixed using zip ties. The camera is to be affixed using glue.

Front Panel
Figure 3: the front panel. The mounted components (from left to right): USB-C socket, power switch, start/stop switch.

Camera Hole
Figure 4: the camera hole, which is located on the panel facing away from the rider during use.

Full RRSA
Figure 5: the full assembly with annotations.

Speed Sensor
Figure 6: detail on the speed-sensing portion of the assembly. The reed switch will be secured using two zip ties.

### Analysis:

**A1.1. Pressure Sensor:** 

    Imprecision = 2 cm < 4.67 cm
    Operating range: 300 hPa to 1200 hPa
    Measurement time [high precision] = 105 ms [4]
    Maximum sample rate = 1 ÷ 105 ms = 9.524 Hz > 2 Hz

**A1.2. Speed Sensor:**

    Raspberry Pi GPIO sampling speed = 10 MHz [6] > 9.6 Hz

**A2.1. Video Data Syncing:**

    Raspberry pi time clock rate = 1 MHz
    Time precision = 1 μs
    Max frame desync = 1 μs ÷ (1 ÷ 60 Hz) × 100 % = 0.006 %

**A2.2. Video Quality and Format:**

    Camera recording quality: 720p, 60 fps (or below) [as specified]
    Connection protocol: Rasberry Pi CSI (camera serial interface)
    Formatting capability: MPEG-4 h.264 via ffmpeg

**A4. Recording Capacity:**

    Storage capacity: 128 Gb
    Typical bitrate for as-specified video: 6.5 MB/s [7]
    Video-specific storage = 6.5 MB/s × 60 s/min × 60 min/h × 3 h = 70.2 GB
    Remaining storage = 128 Gb - 70.2 Gb = 57.8 Gb

The remaining storage is the be put to use for sensor data and the operating system.
The SD card used for storage is V10 compliant; rated to record full HD video.

**A3: Battery Life:**

    Raspberry Pi Zero 2W current requirement [stressed] = 580 mA [1]
    Raspberry Pi Camera current requirement [max] = 250 mA [2]
    Raspberry Pi GPIO internal pullup resistor = 33-73 kΩ [3]
    Raspberry Pi logic level = 3.3 V
    Reed switch current draw = 3.3 V / 33 kΩ = 0.1 mA
    DPS310 altitude sensor current draw [max] = 0.345 mA [4]
    Indicator light current draw = 20 mA each [5] = 20 mA × 2 = 40 mA
    Power supply nominal efficiency = 90 %
    Battery energy storage capacity = 24.42 Wh
    Effective battery energy = 24.42 Wh × 90 % = 21.98 Wh
    RRSA power requirement [max] = 5 V × (580 mA + 250 mA + 0.1 mA + 0.345 mA + 40 mA) = 4.352 W
    Projected battery life = 21.98 Wh ÷ 4.352 W = 5.050 hours > 3 hours

Also:

    Recommended constant battery discharge rate = 0.25 C = 1.32 A
    Projected current draw [max] = (4.352 W ÷ 90 %) ÷ 3.7 V = 1.31 A < 1.32 A
    Battery charge rate specification = 1.5 A
    Charge rate limit = 1 A < 1.5 A

**A5. Useability:**

Two button interface; one to turn off and on, the other to start or stop the video recording. The power button has an LED that signifies power on, and the other LED lights when video is being recorded and blinks during data transfer.

**A6. Durability:**

Waterproof box provides protection from weather conditions. Aside from the fasteners shown in figures 2,4,6 [nuts and bolts], glue will be used to seal the entry hole for the speed sensor wires as well as the hole for the camera; zip ties will be used to attach the speed sensing reed switch and the battery.

A7. Device Fitment: The housing attaches to the handlebars using a mechanical twist-locking mechanism and a screw-tensioned ring with rubber adaptors. The bracket requires no tools for removal or installation of the box, and the rubber adapters allow for universal fitment.

**Table 1:** Bill of Materials.
| Subsystem Name: | Ride Data Acquisition System | | | | | | | |
| --- | --- | --- | --- | --- | --- | --- | --- | --- |
| Requested by: | Tyler C. | | | | | | | |
| Approve by: | | | | | | | | |
| Total Cost: | $174.78 | | | | | | | |
| | | | | | | | | |
| | | | | | | | | |
| Level | Part # | Part Name | Supplier | Supplier Part # | Qty | Units  | Unit Cost | Cost |
| 1 | COMP1 | Raspberry Pi Zero 2W | Digikey | 2648-SC0510-ND  | 1 | Module | $15.00 | $15.00  |
| 1.1 | MEM1 | 128 GB Micro SD Card | Newegg | N82E16820215186 | 1 | Module | $10.49 | $10.49  |
| 2 | PSU1 | Power Supply | NONE | NONE | 1 | Assy | | $0.00 |
| 2.1 | MD1 | Adafruit Powerboost 1000 | Adafruit | 2465 | 1 | Module | $19.95 | $19.95  |
| 2.2 | CABLE1 | AK67421-0.3-VM | Digikey | AE11229-ND | 1 | Piece  | $2.58 | $2.58 |
| 2.3 | JACK1 | USB C Jack to USB A Jack Round Panel Mount Adapter | Adafruit | 4259 | 1 | Piece  | $5.95 | $5.95 |  
| 2.4 | CABLE2 | USB cable - 6" A/MicroB | Adafruit | 898 | 1 | Piece  | $2.95 | $2.95 |
| 2.5 | SW1 | Rugged Metal On/Off Switch with Green LED Ring - 16mm Green On/Off | Adafruit | 482 | 1 | Piece  | $4.95 | $4.95 |
| 2.6 | SW3 | Rugged Metal Pushbutton with Red LED Ring - 16mm Red Momentary | Adafruit | 559 | 1 | Piece  | $4.95 | $4.95 |
| 2.7 | BT1 | Lithium Ion Battery Pack - 3.7V 6600mAh | Adafruit | 353 | 1 | Piece  | $24.50 | $24.50  |
| 3 | SENSE1 | Speed Sensor | NONE | NONE | 1 | Assy | | $0.00 |
| 3.1 | SW2 | Hamlin SPST - N.O. High Quality Reed Switch | Electronics Goldmine | G26522 | 1 | Piece  | $2.49 | $2.49 |
| 3.3 | ZT1 | Amazon Basics Multi-Purpose Cable Ties - 4-Inch/100mm, 200-Piece, White | Amazon | DS-SZS-002 | 1 | Piece  | $4.62 | $4.62 |
| 3.4 | MAG1 | Bike Wheel Spoke Computer Magnet | AliExpress | NONE | 1 | Piece  | $1.68 | $1.68 |
| 4 | SENSE2 | Adafruit DPS310 Precision Barometric Pressure / Altitude Sensor | Adafruit | 4494 | 1 | Module | $6.95 | $6.95 |
| 5 | MECH1 | Mechanical Parts | NONE | NONE | 1 | Assy | | $0.00 |
| 5.1 | BOX1 | QILIPSU Clear Hinged Cover 220x170x110mm Junction Box | Amazon | B087F9TS25 | 1 | Piece  | $29.99 | $29.99  |
| 5.2 | MNT1 | Bike Phone Mount, Bicycle Cell Phone Holder with Universal Adapter | Amazon | B08R5K29BC | 1 | Kit | $19.98 | $19.98  |
| 5.3 | FASTENER1 | M2.5-0.45 x 10 mm Zinc Plated Steel Machine Screws (25-Pack) | Home Depot | 311229794 | 1 | 25-Pk  | $6.04 | $6.04 |
| 5.4 | FASTENER2 | M2.5-0.45 Zinc-Plated Metric Hex Nut (5-Piece per Bag) | Home Depot | 204836094 | 3 | 5-Pk | $1.25 | $3.75 |
| 5.5 | FASTENER3 | Gorilla Max Strength Clear Construction Adhesive | Amazon | B0916KZ598 | 1 | Piece  | $7.96 | $7.96 |
| 6 | CAM1 | Camera Module for Raspberry Pi Zero | Pimoroni | CAM003 | 1 | Assy | $10.56 | $10.56  |
| | | | | | | | Total | $174.78 |

### References

[1] L. Pounder, “Raspberry Pi Zero 2 W review: The long awaited sequel,” tomshardware.com, 28-Oct-2021. [Online]. Available: https://www.tomshardware.com/reviews/raspberry-pi-zero-2-w-review. [Accessed: 20-Nov-2022].

[2] jamesh, “Re: Raspberry Pi - camera, reducing power consumption,” Raspberry Pi Forums - Index page, 30-Jul-2011. [Online]. Available: https://forums.raspberrypi.com/viewtopic.php?t=152864. [Accessed: 13-Jan-2023].

[3] A. Scheller, K. Rijnieks, and A. Allan, “Alternative Functions,” Raspberry Pi Documentation. [Online]. Available: https://www.raspberrypi.com/documentation/computers/raspberry-pi.html#alternative-functions. [Accessed: 13-Jan-2023].

[4] “DPS310,” infineon.com, 15-Oct-2020. [Online]. Available: https://www.infineon.com/dgdl/Infineon-DPS310-DataSheet-v01_02-EN.pdf?fileId=5546d462576f34750157750826c42242. [Accessed: 14-Oct-2023].

[5] “Rugged metal on/off switch with Red Led Ring: Technical Details,” adafruit.com. [Online]. Available: https://www.adafruit.com/product/916#technical-details. [Accessed: 13-Jan-2023].

[6] M4H, "Maximum theoretical GPIO sample speed," Raspberry Pi Forums. [Online]. Available: https://forums.raspberrypi.com/viewtopic.php?t=128387. [Accessed: 5-Feb-2023]

[7] “A beginner’s guide to bit rate,” adobe.com. [Online]. Available: https://www.adobe.com/creativecloud/video/discover/bit-rate.html. [Accessed: 22-Nov-2022].

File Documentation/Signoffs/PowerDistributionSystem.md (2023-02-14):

Team 4 – Mario Kart & Ride Replay Simulator

Team Member: Ray Durlin

Detail Design: Main Power Distribution System

<br/><br/>

**Function of the Subsystem:** 

The function of the main power distribution subsystem is to receive an incoming power supply from a 120 Vac, 60 Hz, from a wall receptacle and then 
distribute the power through a protected circuit to multiple devices, which carry varying voltage requirements. The following devices that are to 
receive power from the power distribution subsystem are listed below: 
<br/><br/>
•	5 Vdc

&nbsp;&nbsp;&nbsp;&nbsp; o	Main Controller, MET System (User interface), Fan 1, Fan 2, Arduino 1, and Arduino 2

•	12 Vdc

&nbsp;&nbsp;&nbsp;&nbsp;o	Linear Motor

•	15 Vdc

&nbsp;&nbsp;&nbsp;&nbsp;o	Nintendo Switch

•	120 Vac 

&nbsp;&nbsp;&nbsp;&nbsp;o	Display Monitor

<br/>

The wall receptacle provides power via a ground fault circuit interrupter (GFCI) power cord and then goes through an on/off switch located on the 
distribution enclosure. The power is then routed through a 4-amp circuit breaker. Lastly, the protected 120 Vac power branches to the simulator 
display monitor and three AC/DC power supplies, which feed the 5 Vdc, 12 Vdc, and 15 Vdc devices within the Mario Kart simulation bike. 

The power distribution subsystem is to be enclosed in an aluminum enclosure, which is designed within the power distribution subsystem. The power 
distribution enclosure is to house the user interface screen (HMI), cooling fans, on/off switch, (3) power supplies, and (4) microcontrollers. The 
front panel of the enclosure is to be removable for access and house the HMI display.

<br/><br/><br/><br/>

**Constraints:** 

*Constraints are listed in number for Analysis reference.*
<br/><br/>

*Circuit Design:* 

C1. Each power supply is to be adequately sized to be capable of carrying the maximum power requirement for all the devices within its respective circuit.

C2. All wire sizing is to be in accordance with National Electrical Code Article 210.19(A)(1) based on continuous circuit load [1].

C3. The system will maintain overprotection of the Mario Kart simulator devices with a rating of no less than %125 percent of maximum continuous circuit load as specified by 
the National Electrical Code Article 210.20(A) [1]. 

<br/><br/>

*Safety:* 

C4. All 120 Vac terminals within the user interface are to have been covered and contain a warning of electrocution on the cover. 

C5. Power subsystem must include a means of de-energizing the system via circuit breaker lockout. 

C6. Circuit to include GFCI to ensure that all devices within the Mario Kart simulation are properly protected from ground faults. 

<br/><br/>

*Enclosure:* 

C7.  The enclosure is to be sized to house all devices within the subsystem, excluding incoming and outgoing power cabling.

C8. The front panel containing the HMI is to be removable for access. 

C9. The enclosure is to be fully enclosed and free of any openings. 

C10.  The enclosure is to be properly grounded for protection to protect equipment and possible electrical shock.

<br/><br/>

**Buildable schematic:**



Figure 1. Power Distribution Wiring Diagram

<br/><br/>



Figure 2. Power Distribution Model - Right Side
<br/><br/>



Figure 3. Power Distribution Model - Left Side
<br/><br/>

<br/><br/>

<br/><br/>

**Analysis:**
<br/><br/>
*Analysis is listed in order of constraint reference.*

<br/><br/>

*Circuit Design:*

Devices to be powered within the subsystem below in table 1: 

<br/>

Table 1:

| Circuit Number | Device | Voltage (V) | Voltage Type (AC or DC) | Max Current (A) | Max Power (W) |
|---|---|---|---|---|---|
| 1 | Main Controller | 5 | DC | 3 | 15.00 |
| 1 | MET System (User interface) | 5 | DC | 3 | 15.00 |
| 1 | Fan 1 | 5 | DC | 0.25 | 1.25 |
| 1 | Fan 2 | 5 | DC | 0.25 | 1.25 |
| 2 | Linear Motor | 12 | DC | 3.4 | 40.80 |
| 3 | Nintendo Switch | 15 | DC | 2.10 | 31.50 |
| 4 | Display Monitor | 120 | AC | 0.29 | 35.00 |

<br/><br/>

A1. **Power Supply Sizing:** Based on the power consumption of all devices in table 1, the power supplies are 45 Watts for both the 5 Vdc and 15 Vdc circuits, while the 12 
Vdc circuit power supply is rated for 60 Watts.

Calculation:

120 Vac/5 Vdc Power Supply maximum power = 32.50 W (6.5 A * 5 Vdc)

120 Vac/12 Vdc Power Supply maximum power = 40.80 W (3.4 A * 12 Vdc)

120 Vac/15 Vdc Power Supply maximum power = 31.50 W (2.1 A * 15 Vdc)
<br/><br/>



Figure 4. DC Power Model.
<br/><br/>

A2. **Wire sizing:** The highest rated current devices powered within this subsystem are the linear motor actuator, which has a rating of 3.4 Amps. The design is to use 14 
Gauge THHN stranded rated at 15 Amps, which is at least %125 of the continuous load rating specified in National Electrical Code Article 210.19(A).

A3. **Overprotection rating:** A single 3 Amp circuit breaker is to be upstream of each power supply (manufacturer recommends 3.15 slow blow fuse). Based on the power supply 
circuit protection of 3 Amps each and the maximum current rating of the display monitor, a 15 Amp circuit breaker is to be used to protect the whole system. The 
overprotection device also meets the %125 NEC requirements specified in the National Electrical Code Article 210.20 (A).

Calculation:

(3 A * 3) + 0.29 = 9.29 A

9.74 A * %125 = 11.61 A

<br/><br/>

*Safety Designed:*

A4. **120 Vac Terminals:** All 120 Vac terminals are covered within the enclosure using plexiglass covering with a hazardous warning sticker visible. The hazardous warning is 
to be similar in design to the label represented below in Figure 5. 

<br/><br/>

<br/>
Figure 5. Danger Sign for 120 AC cover.
<br/><br/>

A5. **Means of De-Energizing:** The means of de-energizing the power distrubution subsystem is by removing the power plug from the wall receptable. The power plug is to be 
removed from a wall receptable any time that a power distribution panel is removed.

A6. **Ground Fault Protection:** Additional protection was designed regarding safety using a Ground Fault Circuit Interrupter (GFCI), which is built into the incoming power 
cord of the Mario Kart Simulator. 

<br/><br/>

*Enclosure Design:*

A7. **Enclosure Sizing:** The enclosure is increased from previous design to 12” x 12” x 6” for which to provide a minimum of 2” clearance between all devices and the front 
panel for accessibility. 

A8. **Front Panel Access:** The enclosure includes 4 removeable fasteners to remove the front panel for access. 

A9. **Enclosure Quality:** The enclosure is pre-formed and manufactured by Hammond Manufacturing without any openings and cable clamps are to be used to seal power cable 
input 
and outputs. EPDM rubber is used to create a seal between HMI and inside of front panel.

A10. **Grounding:** Enclosure to be grounded using grounding bar representing in wiring schematic. 

<br/>
<br/>
<br/>
<br/>

**BOM:**
<br/><br/>
| Level | Part # | Part Name | Supplier | Supplier Part # | Qty | Units | Unit Cost | Cost |
|---|---|---|---|---|-----|---|---|---|
| 1 | Enclosure Assembly  | | | | | | | |
| 1.1 | ENCL1 | BOX STEEL GRAY 12"L X 12"W | Digikey | CS12126 | 1 | ea. | $39.65 | $39.65  |
| 1.2 | CBLCLMP-5 | 5-Pack Cable Clamp | Home Depot | 100186543 | 1 | ea. | $4.34 | $4.34 |
| 1.3 | PLXGLS2 | 11 in. x 14 in. x .093 in. Acrylic Sheet | Home Depot | 202090111 | 1 | ea. | $8.28 | $8.28 |
| 1.4 | DINRAIL | TS35 Din Rail 35mm x 7.5mm | DigiKey | ADR3575-U7874-ND | 1 | ea. | $7.06 | $7.06 |
| 1.5 | EPDM | EPDM 1/8 in. x 36 in. x 96 in. Commercial Grade 60A Rubber Sheet | Home Depot | 303371976 | 1 | ea. | $0.00 | $0.00 |
| 2 | Electrical Assembly | | | | | | | |
| 2.1 | PS1 | 120 VAC / 5 VDC Power Supply | DigiKey | 102-PSK-45-5-DIN-ND  | 1 | ea. | $22.65 | $22.65  |
| 2.2 | PS2 | 120 VAC/ 12 VDC Power Supply | Mouser | 490-PSK-60-12-DIN | 1 | ea. | $24.93 | $24.93  |
| 2.3 | PS3 | 120 VAC / 15 VDC Power Supply | DigiKey | 102-PSK-45-15-DIN-ND | 1 | ea. | $22.65 | $22.65  |
| 2.4 | SWTCH | 2 Pos Switch | DigiKey | Z6183-ND | 1 | ea. | $15.89 | $15.89  |
| 2.5 | 14GACONN | 16 - 14 AWG #8 - 10 Stud Size Vinyl-Insulated Spade Terminals, Blue (15-Pack) | Home Depot | 202522889 | 1 | ea. | $3.63 | $3.63 |
| 2.6 | CB-3A | CIRCUIT BREAKER 3A | DigiKey | 277-17752-ND | 3 | ea. | $19.00 | $57.00  |
| 2.7 | 14WIRE | 25 ft. 14 Black Solid CU THHN Wire | Home Depot | 301210609 | 1 | ea. | $0.00 | $0.00 |
| 2.8 | GRDBAR | 4 Terminal Grounding Bar | Home Depot | 100207842 | 1 | ea. | $8.31 | $8.31 |
| 2.9 | GFCI-15 | 15 Amp Compact Right Angle Plug-In GFCI, Black | Home Depot | 205189963 | 1 | ea. | $21.99 | $21.99  |
| 2.10  | WARNLAB | 120 VAC Warning Label | None | None | 1 | ea. | $0.00 | $0.00 |
| 2.11  | TRMBLK | Terminal Block | DigiKey | 277-2026-ND | 10  | ea. | $1.53 | $15.30  |
| 2.12  | TRMJMP | 3 Pos - Terminal Block Jumper | DigiKey | 277-3230-ND | 3 | ea. | $1.80 | $5.40 |
| 2.13  | CONN1 | Linear Motor Control Connector | TME | XT30U-F | 1 | ea. | $0.45 | $0.45 |
| 2.14  | CBMAIN-1 | CIRCUIT BREAKER 15A | Digikey | 277-17761-ND | 1 | ea. | $19.00 | $19.00  |
| 2.15  | TERMSTP4 | 4 Lug Terminal Strip | DigiKey | A98505-ND | 4 | ea. | $2.94 | $11.76  |
| | | | | | | | Total | $288.29 |

<br/><br/>

**References**

[1]    NFPA Link®. [Online]. Available: https://link.nfpa.org/free-access/publications/70/2023. [Accessed: 19-Nov-2022].

<br/><br/>

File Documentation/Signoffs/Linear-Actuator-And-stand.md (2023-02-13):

Team 4 – Mario Kart & Ride Replay Simulator

Team Member: Ray Durlin, Blake Pickett, Tyler Chittum, Benjamin Reed, and Sage Mooneyhamm

Detail Design: Linear Actuator and Stand

<br/><br/>

**Function of the Subsystem:** 
<br/><br/>
The function of the linear actuator stand subsystem is to provide a base for the linear actuator during Mario Kart gameplay and ride replay simulations. The linear actuator 
stand will also house the linear actuator controller. The function of the linear actuator stand is to provide a base for the linear actuator during Mario Kart simulations. 
The linear actuator stand also houses the linear actuator controller. The linear motor’s function is to receive input from the motor control subsystem and provide a feedback 
system to the control.
<br/><br/>

**Constraints:**

<br/><br/>
**Anchoring:** The linear actuator is secured in a manner that the actuator and stand are anchored.

**Grounding:** The case of the linear actuator is to be properly grounded.

**Sizing:** The linear actuator stand is to be sized for the motor controller to be stored inside of the stand.

**Openings:** The linear actuator stand has two openings for the power and control wires from the controller to the actuator. 

**Constructions:** The linear motor stand is to be constructed of materials that will not shield wireless communications of the motor controller. 

<br/><br/>
**Buildable schematic:**

<br/><br/>



<br/>
Figure 1. Right View of 3D model for the Linear Actuator Stand Subsystem
<br/><br/>


<br/>
Figure 2. Rear View of 3D model for the Linear Actuator Stand Subsystem
<br/><br/>


<br/>
Figure 3. Full View of 3D model for the Linear Actuator Stand Subsystem

<br/><br/>
<br/><br/>

**Analysis:**

<br/><br/>

**Anchoring:** The linear actuator is mounted to the stand, which is anchored to the bike stand frame using clamps, and is represented in Figures 1, 2, and 3. The bike 
frame height has a clearance of 10mm, but is also adjustable to endure clamps fits around frame and between the floor.

**Grounding:**  The linear actuator case is grounded to the bike stand frame using 14 Gauge THHN stranded wire, rated for 15 Amps. Paint is to be removed from bike stand 
frame and is represented in Figure 2. 

**Sizing:** The linear actuator stand modeled to be 5.6” x 5.8” x 6.3”, which is capable of containing the controller board that is approximately 3.5” x 2”, while 
maintaining the height required for the resistance subsystem.

**Openings:** Figure 2 shows 2 holes, one circular for power input, and the other a slit opening for the actuator to controller communication/power.

**Constructions:** The linear actuator stand is constructed using 0.5” thick plexi-glass material that will not block communication from the linear actuator controller to 
the main controller.

<br/><br/>
<br/><br/>
**BOM:**
<br/><br/>
The bill of materials (BOM) to accomplish the design illustrated in the schematics is provided in Table 1. 
<br/><br/>
Table 1.

| Level | Part # | Part Name | Supplier | Supplier Part # | Qty | Units | Unit Cost | Cost |
|---|---|---|---|---|-----|---|---|---|
| 1 | LINMOTOR100 | Linear Motor | Pololu | 4953 | 1 | ea. | $183.95 | $183.95 |
| 2 | SCR3 | #3 x 1/2 in. Phillips Head Brass Wood Screw (6-Pack) | Home Dept | 204587520 | 1 | bag | $1.38 | $1.38 |
| 3 | PLXGLS | 20 in. x 32 in. x 0.093 in. Acrylic Sheet | Home Dept | 202038049 | 1 | ea. | $25.48 | $25.48  |
| 4 | CBLCLMP1 | CBL CLAMP P-TYPE BLACK FASTENER | DIGIKEY | N-32B-BK | 2 | ea. | $1.20 | $2.40 |
| 5 | 14WIRE | 25 ft. 14 Black Solid CU THHN Wire | Home Depot | 301210609 | 1 | ea. | $0.00 | $0.00 |
| 6 | 14GACONN | 16 - 14 AWG #8 - 10 Stud Size Vinyl-Insulated Spade Terminals, Blue (15-Pack) | Home Depot | 202522889 | 1 | ea. | $3.63 | $3.63 |
| 7 | SCR2 | #2 x 1/4 in. Phillips Flat Head Zinc Plated Wood Screw (8-Pack) | Home Dept | 204587381 | 4 | bag | $1.38 | $5.52 |
| 8 | LNMTCLP | Routing Clamp | McMaster Carr | 3039T16 | 3 | ea. | $2.92 | $8.76 |
| 9 | BRKPLT | 12 in. x 12 in. 22-Gauge Weldable Sheet | Home Dept | 100237896 | 1 | ea. | $13.57 | $13.57  |
| 10 | AXLMNT | 10mm Universal Aluminum Mounting Hubs for Shaft – 18009 | OzRobitics | 18009 | 1 | ea. | $9.40 | $9.40 |
| | | | | | | | Total | $254.09 |

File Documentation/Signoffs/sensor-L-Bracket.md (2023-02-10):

# Steering L-Bracket Subsystem 
## Team 4 - Blake Pickett ##

_Function of the Subsystem:_

Modifications to the Steering L-Bracket Subsystem will provide stabilized support to ensure that the Gear attached to the Potentiometer meshes with the Gear attached to the handlebars. Both Gears mesh in order for the Mario Kart Bike to perform as designed. The purpose or function of the modifications to the Steering L-Bracket Subsystem is to replace the plastic 3D printed L-Bracket with a metal component and properly attach it to the Mario Kart Bike’s steering column. These revisions will stabilize the Steering Subsystem and increase steering fidelity while creating a form that is more like commercial products.  

_Constraints:_ 

**Increased Fidelity:** The Steering L-Bracket mechanism shall be strengthened using a metal component. 

**Adaptability to Steering Column:** The L-Bracket must be positioned more than 0.25 inches off the steering column. 

_Buildable Schematic:_

**Figures 1**, **2**, and **3** show a 3D model of the Steering L-Bracket Subsystem.



**Figure 1.** 3D Model of Steering L-Bracket



**Figure 2.** 3D Model of Steering L-Bracket



**Figure 3.** 3D Model of Steering L-Bracket

_Analysis:_ 

An analysis has been performed to determine the performance of the existing Steering Subsystem. The results of the analysis and visual inspection indicate that the existing L-Bracket cannot perform as intended. The L-Bracket must be strengthened rather than simply re-placed with a new plastic 3D printed component. The analysis verified that the Steering L-Bracket must be fabricated from metal rather than plastic, and it must be properly secured to the Mario Kart Bike. 

Although analysis indicated that the existing clamps did not break while in use for the previous design, they were not an effective means of attaching/stabilizing the Steering L-Bracket to the steering column because the L-Bracket came in contact with the rubber seal on the Mario Kart Bike’s steering column. Therefore, the clamps must be replaced with conduit hangers to hold the L-Bracket off the surface of the steering column in order to clear the rubber seal.

Specifically, modifications include strengthening the Steering L-Bracket mechanism using a new stainless-steel L-Bracket measuring 12 inches by 7 inches by 2 inches to replace the plastic 3-D printed component. The new metal Steering L-Bracket will be attached to the steering column using two 1-inch conduit hangers. A diagram of the conduit hangers is provided in **Figure 4** [1]. Two holes will be drilled in the L-Bracket, so it can be bolted to the conduit hangers. 

Incorporating a commercially available L-Bracket is a cost-effective solution for providing the necessary strength and stability. Conduit hangers are also commercially available at a minimal cost. 



**Figure 4.** Diagram of Conduit Hanger [1]

_BOM:_

The bill of materials (BOM) to accomplish the design illustrated in the 3D Model is provided in **Table 1**. 

**Table 1.** Bill of Materials
| Brand / Manufacturer | Part Name | Supplier | Part / Model # or ASIN # | Qty | Units  | Unit Cost | Cost |
| --- | --- | --- | --- | --- | --- | --- | --- |
| Ekena Millwork | 12-in x 2-in x 7-in Stainless Steel Support Bracket| Lowe’s | BKTM02X12X07HSCRS | 1 | Pieces | $15.24 | $15.24 |
| Sigma ProConnex | 1-in Steel Conduit Hangers | Lowe’s | 49120 | 2 | Pieces | $0.98 | $1.96  |
| Hillman | 1/4-in- 20 x 1-in Phillips-Drive Machine Screws | Lowe’s | 490435 | 1 | Pack | $1.38 | $1.38  |

**References** 

[1]  _Sigma Proconnex 1-in Schedule 40 schedule 80 zinc-plated steel conduit ..._ (n.d.). Retrieved February 8, 2023, from https://www.lowes.com/pd/Sigma-Electric-ProConnex-1-in-Conduit-Hangers-Schedule-40-PVC-Compatible-Schedule-80-PVC-Compatible-Intermediate-Metal-Conduit-Compatible-Ga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

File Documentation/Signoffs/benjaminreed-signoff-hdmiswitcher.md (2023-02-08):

Team 4 -- Mario Kart & Ride Replay Simulator

Team Members: Ray Durlin, Blake Pickett, Tyler Chittum, Benjamin Reed, and Sage Mooneyham

Detail Design: HDMI Switcher

*Function of the Subsystem:*

The HDMI Switcher is designed to allow users to connect the HDMI ports for their Nintendo Switch and their RRS kit into a single HDMI input to their television or monitor. The switcher that will be used is the BENFEI single-button HDMI switcher (BHS) retrofitted with a Fujitsu NAL-12W-K relay as the switching mechanism. A 1N5818 Diode will protect the This switcher will be installed in the touchscreen compartment and connected to the Raspberry Pi (RPi). If the control bits can be accessed, the Raspberry Pi will interface with a relay to switch between the bits. The button will be replaced by a single pole single throw relay with the switch input originating from a RPi GPIO pin. A 1N5818 diode will protect the RPi from back EMF resulting from the de-energizing of the relay coil [3].

*Constraints:*

*HDMI Compatibility:* The BHS must be rated for 1080p resolutions.

*HDMI Quantity:* The switcher must have at minimum two input HDMI ports and one output HDMI port.

*Relay Voltage/Current Ratings:* The relay coil must be rated for 3.3 V and a maximum 16 mA, and the relay must operate at 3.3 V or below.

*Relay Power Rating:* The power dissipation at the relay coil cannot exceed 70 mW.

*Back EMF Accommodations:* A diode must be implemented in parallel with the relay coil to protect the RPi from back EMF that results from de-energizing the coil [3].

*Background*

As HDMI is standard in the modern era, the multiplexer needs to be compatible with such an input. The RRS Acquisition is designed to record video at a resolution of 720p. Furthermore, the Nintendo Switch is rated to display data at a resolution of 1080p while in TV mode, which is the mode that the Nintendo Switch will be in while using the bike [1].

The Raspberry Pi supplies 3.3 V [2]. A relay with coil terminals rated for these values are necessary. Additionally, to ensure that the relay functions properly, the "must operate voltage" must be less than 3.3 V. Finally, the RPi is limited to a maximum 16 mA output, so the coil drive current must be less than 16 mA to accommodate
 
*Buildable Schematic:*

Screenshot (96)

The schematic shows how the BHS button ports will interact with the relay. However, it is not needed to prove the relay retrofit will work. Relay switches act as a button that completes the circuit when an electrical value is applied to its coil and opens the circuit otherwise. This is identical to how a button works, except the button utilizes the physical depression of the button to complete the circuit. Since these two methods are almost identical in how they connect a circuit, it can easily be inferred that replacing the button with a relay will work.

*Analysis:*

*HDMI Compatability:* The BHS is rated for up to 4K resolutions. This is more than sufficient for the required 1080p resolutions.

*HDMI Quantity:* The BHS is designed as a two-to-one HDMI switcher. This satisfies the two-port constraint.
*Relay Voltage/Current Rating:* The TXS2-L-3V is rated with a must operate voltage of 2.4 V and a maximum voltage of 4.5 V [4]. In addition, the relay current is 11.7 mA, which is rated within the operating range of the RPi.

*Relay Power Rating:* The equation for power is P = I^2^R. In this case, the power is calculated as

P = 0.0117A^2 (257 Ω)

P = 35 mW

Therefore, the relay must be rated for 35 mW. The TXS2-L-3V relay is rated for 70 mW and is therefore sufficient [4]. Additionally, for the 3.3V pulse, the equation is

P = V^2/R

P = 3.3V^2/257 Ω

P = 43 mW

 which also shows the relay rating is sufficient.

*BOM*

| Team 4 - Mario Kart & RRS | Bill of Materials (BOM) | | | | | | | |
| --- | --- | --- | - | - | - | - | - | - |
| Subsystem Name: | HDMI Switcher | |  |  |  |
| Requested by: | Benjamin R | |  |  |  |
| Approve by: | | |  |  |  |
| Total Cost: | $16.69 | |  |  |  |
| | | |  |  |  |  |  |  |
| | | |  |  |  |  |  |  |
| Level | Part # | Part Name | Supplier | Supplier Part # | Qty | Units | Unit Cost | Cost |
| 1 | BHS100 | HDMI Switcher | BENFEI | N/A | 1 | Emb. System | $10.99 | $10.99 |
| 2.1 | RELAY100 | TXS2-L-3V Relay | Digikey | 255-1899-ND | 1 | Piece | $5.30 | $5.30 |
| 2.2 | DIODE100 | 1N5818 Diode | Digikey | 497-4548-1-ND | 1 | Piece | $0.40 | $0.40 |
| | | |  |  |  |  | Total | $16.69 |

REFERENCES

[1] Nintendo, "Technical Specs." nintendo.com. https://www.nintendo.com/switch/techspecs/#switch-section (accessed Nov. 21, 2022).

[2] Raspberry Pi Ltd., "Raspberry Pi 4 Model B." raspberrypi.com. https://datasheets.raspberrypi.com/rpi4/raspberry-pi-4-datasheet.pdf (accessed Nov. 21, 2022)

[3] Durakool, “A Layman’s Guide to Coil Suppression.” Durakoolrelays.com. https://www.durakoolrelays.com/information/technology/layman-s-guide-to-coil-suppression/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,Back%20EMF%20(Electromotive%20Force).

[4] Panasonic, “TX-S Relays.” Panasonic.eu. https://mediap.industry.panasonic.eu/assets/download-files/import/mech_eng_txs.pdf

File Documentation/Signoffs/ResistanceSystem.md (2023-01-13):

Team 4 – Mario Kart & Ride Replay Simulator

Team Members: Ray Durlin, Blake Pickett, Tyler Chittum, Benjamin Reed, and Sage Mooneyham

## Detail Design: Resistance System ##

### Function of the Subsystem:

The function of the resistance system is to control and vary the resistance felt by the user of the Mario Kart Bike, hereafter referred to as the bike.  

- The controller monitors the linear actuator feedback voltage to determine its current position with 10-bit precision, which corresponds to the distance of the magnet array from the flywheel. 

- An external digital input (via the Bluetooth module) is received from the ride replay subsystem to determine the calculated set point which the actuator should extend to. This recieved value corresponds to a resistance state, of which there are 511; the limiting factors being the 10-bit precision of the controller and the usable portion of the actuator's range.

- The controller supplies either a positive or negative voltage to the linear actuator to control the direction of the actuator's motion.

- The actuator is to vary the array of magnets perpendicular to the simulator’s rear conductive flywheel (not the current flywheel on the bike, a new flywheel with dimensions that fit our design more effectively) to generate eddy currents using the primary magnetic induction formed at the conductor [1], which result in the generation of braking torque opposed onto the flywheel. 

- The braking torque will transfer from the flywheel to the rear bike tire, and then from the rear bike tire to the rider’s pedals, which will act to resist the pedaling of the rider. 

### Constraints:

#### Magnet Distance Range: 

- A distance range of 2-25mm from magnet to flywheel was selected, as these distances matched up well with the torque values that we want the resistance system to apply. 

#### Minimum Tire Speed: 

- The minimum speed of the bike tire shall be considered 116.35 rpm. This value is based on the American Council on Exercise's recommendation for the minimum speed required for moderate exercise on a bike [2]. This correlates to 2501.52 rpm in the flywheel (conversion is explained in later sections). At speeds less than 116.35 rpm, the torque placed on the rider will not be specified to reach any minimum value, and the resulution of the resistance changes within this operating region is not specified.

#### Maximum Tire Speed: 

- The maximum speed of the bike tire shall be considered 288 rpm, a value that comes from the average pedaling rpm (118 rpm) of an elite level cyclist [3] (Wheel to pedal gear ratio = 2.444, so wheel speed = 2.444*pedal speed). This correlates to 6192 rpm in the flywheel due to the the rotational velocity ratio of 43:2 between the flywheel and the wheel. If the user passes this speed, no additional torque will be applied to avoid injury to rider. 

#### Maximum Torque at Minimum Speed: 

- Using the value for tire minimum speed (116.35 rpm), we know that the maximum torque at this speed will be produced when the magnets are closest (2mm). From here, you can find magnetic field felt at the flywheel using equation 2. These values can be plugged into equation 1 to give the torque at the flywheel, which can then be converted to torque at the bike wheel/pedals using the gearing ratios between the components (this is explained in more detail later in the document). Using this logic, we find that the max torque at the minimum speed is 49.23 Nm. 

#### Minimum Torque at Minimum Speed: 

- Using the above logic while setting magnet distance to the furthest value (20mm) and wheel speed to the minimum value, we find the minimum torque at minimum speed is 0.002 Nm. 

#### Maximum Torque at Maximum Speed: 

- Using the above logic while setting magnet distance to the closest value and wheel speed to the maximum value (288 rpm), we find the maximum torque at maximum speed is 121.85 Nm. Safety always being a concern, this force is much lower than what is needed to break any leg bone in the average person. [4] [6]. 

#### Minimum Torque at Maximum Speed: 

- Using the above logic while setting magnet distance to the furthest value and wheel speed to the maximum value, we find the minimum torque at maximum speed is 0.004 N•m. 

#### Resistance Resolution: 

- The resistance system will have a resolution of at least 85 states. 

- The controller will allow for 10-bit resolution or 1024 unique states. 

The linear actuator used has a length of 1.97". In practical usage, we would use 45.97 % of this range, yielding an effective number of states of 470.

Note: The minimum and maximum speeds referenced within this section have been converted to bike tire rpm, so the units of measure are consistent throughout the report. The pedaling speed sourced from the reference was multiplied by the gear ratio from the front to rear sprocket, which was 2.44. The speed of the bike is referred to in the units of bike tire revolutions per minute (rpm). 

### Buildable Schematic:



Figure 1. Resistance System Full View



Figure 2. Close Up of Linear Actuator, Flywheel, Magnet Holder



Figure 3. Close Up of Linear Actuator, Flywheel, Magnet Holder with Different Viewpoint

### Aluminum Flywheel:

•	An aluminum circle with a radius of 101.6 mm (4”) will be cut from a sheet of aluminum material. 

•	A hole will be drilled in the center of the aluminum flywheel. 

•	The steel flywheel on the UNISKY bike stand will be replaced with the new aluminum flywheel. 

&ensp;&thinsp; &ensp;&thinsp; •The bolt holding the steel flywheel will be unscrewed.
   
&ensp;&thinsp; &ensp;&thinsp; •The steel flywheel will be replaced with the aluminum flywheel.
   
&ensp;&thinsp; &ensp;&thinsp; •The bolt will be screwed back into place on the bike stand.
   
•	The drive wheel at the back of the UNISKY bike stand will be screwed into the rear wheel of the bike.

&ensp;&thinsp; &ensp;&thinsp; •	This will ensure maximum transfer of energy when the magnetic breaking occurs to the flywheel. 
   
•	The UNISKY bike stand will come with a magnetic brake which will be removed. 

*Bracket:*

•	For the magnetic portion of the resistance system, two mounting brackets will be welded to a metal block stand.

&ensp;&thinsp; &ensp;&thinsp; • The two mounting brackets will be separated by 246 mm to allow for proper mounting of the linear actuator. 

•	The linear actuator will be hooked to the two mounting brackets. 

•	A 14 mm square bracket will be welded to the circular steel bracket.

•	Two magnets will be attached to the opposite side of the circular bracket using the ferromagnetic properties of the steel to hold the magnets in place.

•	The linear actuator will be attached to the square bracket. 

### Analysis:

#### Method of Data Analysis for Calculating Torque: 
The resistance system is centered on the electromagnetic topic of eddy currents and Lenz’s Law. An equation found in a publication for the Centre for Intelligent Machines that models the function of an eddy current braking system was utilized to determine the attributes of the resistance system components [1]. Specifically, the torque achieved depends on angular speed, as well as magnet distance from the flywheel. The function is shown below. 

 
</br> where, 

σ = Conductivity of flywheel material  (Ω−1m−1) </br>
D=magnet diameter (meters) </br>
d = disc (flywheel) thickness (meters) </br>
B = magnet field strength (Tesla) </br>
R = dist from flywheel center to magnet (m) </br> 
θ = angular velocity (rads/s) </br>

This equation was used to determine the torque produced in the flywheel at varying magnet distances and angular speeds. This torque can then be used to find the torque felt in the bike tire, as well as pedals, by applying the flywheel to tire gear ratio (43:2) or tire to pedal gear ratio (43:18), respectively. The following values were determined from the onset. 

- The bicycle’s wheel radius is a known constant of 0.33 m.  

- The flywheel’s radius is a known constant of 0.1016 m. 

- The flywheel’s thickness is a known constant of 0.0127 m. 

- The magnet’s diameter is a known constant of 0.0508 m. 

- The material for the flywheel is aluminum because aluminum has the highest conductivity for the cost, allowing the resistance system to reach the necessary torque values. Therefore, this value is 3.77*107 (Ωm)-1. 

- The axis-to-pole value was set to be approximately 0.305 m. This distance was determined by the flywheel’s radius minus the maximum radius of the magnet options available. Torque is maximized when the magnets are at the edge of the flywheel. 

#### Method of Data Analysis for Calculating Distance between Magnet and Flywheel (Air Gap):

The magnetic field and angular speed can be considered the varying components in torque calculation.  The angular speed will determine the magnet distance (field strength at the flywheel) needed to produce certain torque states. The resistance system will vary the distance between 2 mm and 25 mm. 

The linear motor will increase or decrease the distance from the aluminum flywheel to the magnet (air gap), resulting in an increase or decrease in the magnetic field the flywheel experiences. The distance to magnetic field relationship can be modeled using Equation 2 below, which was found within the magnet suppliers’ website [5].



where,

μ_o=magnetic permeability in a vaccum (Tm/A)

m = magnetic moment (Am^2 )

r=dist. from magnet to flywheel (m)

Because the x-component of the point of measurement on the flywheel is zero, the total magnetic field at the flywheel is equal to the y-component of the magnetic field. 

Magnetic moment of the magnet can be found using Equation 3 found within the magnet suppliers’ website [5].



where, 

B_(r )= residual field (Gauss)

V = magnet volume (m^3 )

The disk magnets utilized in the analysis are 2 inches in diameter and 0.125 inches in thickness. The supplier part number for K & J Magnetics is DY04-N52 [5]. The magnet used in the analysis was determined based on the supplier’s documented shape and field strength. The optimal shape of the magnet for this analysis is a disk shape. The disk shape allowed the team to apply Lenz’s formula without further adaptation. The DY04-N52 magnets have a surface field of 1795 Gauss, which is the ideal field strength to the torque generated by the eddy currents within the resistance system based on the analysis gathered within this report.

*DY04-N52 Magnet Characteristics:*

•	Residual field provided by the magnet suppliers is14,800 Gauss

•	Volume is calculated to be 1.287E-5 m^3

•	Calculated magnetic moment of 15.158 Am^2 

Note: The calculated distance between the magnets and the flywheel required to control the resistance felt by the user will be calculated by the Ride Simulation System (RSS) processing subsystem and is an external input to the resistance subsystem.

#### Minimum Speed Analysis: 

Objective: To prove that the resistance system can provide and vary torque while the rider is traveling at a minimum speed of 116.35 rpm.  

The plots in Figures 6 and 7 are a representation of provided torque, based on the magnetic field between the magnet and flywheel using Equation 1. 



Figure 4. Torque on Rider at Minimum Speed.



Figure 5. Torque Generated at Flywheel at Minimum Speed.

The analysis validates that the resistance system can provide and vary torque braking torque while operating at the minimum speed of 116.35 rpm, with a distance range of 2-25mm between magnet and flywheel. For the minimum speed analysis, the flywheel speed was calculated at 2501.6. To calculate the flywheel speed, the bike tire rpm was multiplied by 21.5. The value of 21.5 is the gear ratio between the bike tire and the flywheel.  

#### Maximum Speed/Maximum Torque Analysis:

Objective: To prove that the resistance system can provide and vary torque while the rider is traveling at a maximum speed of 288 rpm.



Figure 6. Torque on Rider at Maximum Speed.



Figure 7. Torque Generated at Flywheel at Maximum Speed.

Figures 8 and 9 show the torque generated by the resistance system while the rider is at the maximum speed of 288 rpm. The maximum torque that the resistance system can generate will occur at the maximum speed of the bike, with the closest distance between magnet and flywheel. We can see in Figure 8 that the maximum achieved torque is equal to 121.845 Nm. The increased torque generated is the result of an increase in eddy currents, which is represented in Equation 1 in the form of angular velocity (Rad/s). Analysis validates that the maximum torque that the resistance will provide to the rider is 121.845 N•m 

#### Resistance Resolution Analysis:

•	The torque values were calculated by determining incline angle, denoted α, increases that resulted in 10 % increases – give or take 3-4 % – in resistance, given by sin(α), for a range of 0° to 40°. This was done in accordance with the previous specifications proposed for this project.

•	The torque values were determined by scaling the resistance values by that of the 85th state, then multiplying all values by 28.9 Nm to find fractions of our maximum torque.

•	This process was completed using a MATLAB script, which are in the project folder under the name state_test.m. The torque values, in Nm, are shown in Table 1. 

#### Torque Values in Nm at Minimum Speed

| Table 1. | | | | | | | | |
|---|---|---|---|---|---|---|---|---|
| 0.0643 | 0.0693 | 0.0742 | 0.0841 | 0.0940 | 0.1039 | 0.1138 | 0.1237 | 0.1336 |
| 0.1435 | 0.1583 | 0.1732 | 0.1880 | 0.2029 | 0.2177 | 0.2375 | 0.2573 | 0.2771 |
| 0.2969 | 0.3216 | 0.3463 | 0.3711 | 0.4008 | 0.4305 | 0.4651 | 0.4997 | 0.5393 |
| 0.5789 | 0.6234 | 0.6679 | 0.7174 | 0.7718 | 0.8262 | 0.8856 | 0.9499 | 1.0192 |
| 1.0934 | 1.1725 | 1.2566 | 1.3456 | 1.4445 | 1.5484 | 1.6572 | 1.7759 | 1.9044 |
| 2.0379 | 2.1813 | 2.3345 | 2.5025 | 2.6804 | 2.8681 | 3.0706 | 3.2879 | 3.5198 |
| 3.7666 | 4.0329 | 4.3189 | 4.6244 | 4.9494 | 5.2988 | 5.6725 | 6.0704 | 6.4974 |
| 6.9533 | 7.4428 | 7.9657 | 8.5268 | 9.1256 | 9.7667 | 10.454 | 11.188 | 11.972 |
| 12.811 | 13.712 | 14.674 | 15.705 | 16.808 | 17.989 | 19.249 | 20.599 | 22.041 |
| 23.586 | 25.239 | 27.007 | 28.901 | | | | | |

In order to find the minimum change in torque required for the design, the values of torque up to the maximum torque attainable at the minimum speed was calculated via the prior algorithm. The smallest change in torque present within the resulting list was 0.0084 N•m, which corresponds to the very first two states in the list. The difference in torque corresponding to the difference in distance between the furthest two possible positions which the controller can set the actuator in a range extending from 2 mm to 25 mm is 0.141 micro N•m.

#### Torque Values in Nm at Maxium Speed

| 0.2712 | 0.292 | 0.3129 | 0.3546  | 0.3963  | | |
|---|---|---|---|---|---|---|
| 0.4381 | 0.4798 | 0.5215 | 0.5632  | 0.6049  | 0.6675  | 0.7301  |
| 0.7927 | 0.8553 | 0.9179 | 1.0013  | 1.0847  | 1.1682  | 1.2516  |
| 1.3559 | 1.4602 | 1.5645 | 1.6897  | 1.8148  | 1.9608  | 2.1069  |
| 2.2737 | 2.4406 | 2.6283 | 2.8161  | 3.0246  | 3.2541  | 3.4835  |
| 3.7338 | 4.0049 | 4.2969 | 4.6098  | 4.9434  | 5.2979  | 5.6733  |
| 6.0903 | 6.5282 | 6.9869 | 7.4872  | 8.0292  | 8.592 | 9.1964  |
| 9.8424 | 10.5508  | 11.3007  | 12.0922 | 12.9459 | 13.8619 | 14.84 |
| 15.8802  | 17.0031  | 18.2087  | 19.4967 | 20.8671 | 22.3402 | 23.9158 |
| 25.5935  | 27.3937  | 29.3157  | 31.3795 | 33.5843 | 35.9497 | 38.4743 |
| 41.1772  | 44.0768  | 47.1708  | 50.4765 | 54.0107 | 57.809  | 61.8656 |
| 66.2133  | 70.8628  | 75.8423  | 81.157  | 86.8467 | 92.9265 | 99.4416 |
| 106.4082 | 113.8654 | 121.8499 | | | | 

Table 2

The table above showcases 85 states of resistance, utilizing a variance of magnet distance to flywheel. From these two tables, we can see that at least 85 states of resistance can be created at any speed, simply due to the linear actuator being able to provide 85 different magnet distances, regardless of speed.
</br>
</br>

*Control Circuit Components Analysis:*

An analysis of selected control circuit components and the resultant relevant design considerations are provided in Table 3.

| Table 3: Analysis of Selected Control Circuit Components and Design Considerations | |
|---|---|
| Component(s) | Design Considerations |
| Switching Transistors (Q1, Q2, Q3, Q4) | Q1 and Q2 are rated to handle continuous current up to 24 A, while Q3 and Q4 are rated to handle continuous current up to 45 A; both are well above the expected current requirement. Q1 and Q2 only need to switch when the actuator changes direction, and a delay can be programmatically implemented to ensure no current flows during the switching of these transistors. However, Q3 and Q4 must be able to switch fast enough to handle Pulse Width Modulation (PWM). These FETs have rise and fall times in the order of tens of nanoseconds. As such, they should be easily capable of handling a PWM signal in the kHz range. |
| Back-EMF Protection Diodes (D1, D2, D3, D4) | These diodes are Schottky diodes with fast switching time and very low forward voltage. Compared to the body diodes of the utilized transistors (Vf ~ 1 V), these diodes provide a forward voltage of equal to or less than 0.5 V, effectively bypassing the transistors during reverse-conduction. These diodes are specified for use in free-wheeling applications in the datasheet and are well-suited to handle the large momentary current spikes produced by back-EMF, given that they are rated to handle 100 A peak current. |
| Resistors (All) | All resistors in this circuit were subject to only very small power dissipations: less than a milliwatt in all cases. As such, small, common ¼ W resistors were selected. Gate resistors were selected to be surface mount chip-resistors to minimize space usage. The gate driver resistors for the P-Ch FETs are larger than those for the N-Ch FETs, as switching speed is not a priority for the P-Ch FETs. The PWM will be done on the N-Ch FETs, and it is vital that the voltage drop across the gate driver IC be minimized to ensure complete biasing at steady-state. |
| Pre-Biased Dual NPN IC (U1) | This component is used to bias the gates of the P-Ch FETs, as turning these transistors off will require a voltage of 12 V – a voltage not achievable by using the microcontroller alone. This component was selected because it combines the utility of four resistors and two BJTs into a single package. |
| Arduino Nano (A1) | This microcontroller module was selected because it is already in our stock. It provides an on-board voltage regulator capable of regulating to 3.3 V and to 5 V. The 3.3 V supply is ideal for powering the selected wireless module, while the 5 V supply is ideal for providing a logic-voltage reference to the linear actuator feedback. |
| Bluetooth Module | The HC06 module is an incredibly cheap Bluetooth module. It should be capable of providing the required range, as it has a maximum range of about 10 m. In addition to being inexpensive, this module also has the benefit of being very easily connected; it requires only four pins to be connected to the external circuit. |
| Power Connector | The component handles the power input to the circuit, which is then fed into the linear actuator. As such, it must be rated to handle several amperes of current. An XT30 connector was selected, as this type is rated for 15 A which is well over the expected current demand; it does not allow the user to connect the polarity incorrectly. In addition, the mating connector is commonly available in a form that lends itself to the easy fabrication of cables of a custom length without any special equipment. |

*Abbreviation Definitions:*

•	3D: three dimensional

•	RPM: revolutions per minute

•	FET: field effect transistor

•	P-Ch: P-channel

•	N-Ch: N-channel

•	PWM: Pulse-width modulation

•	EMF: electromotive force; a potential difference

•	IC: integrated circuit

•	BJT: bipolar junction transistor

### BOM:

| Team 4 - Mario Kart & RRS | | Bill of Materials (BOM) | | | | | | |
|:---:|:---:|---|---|---|-----|---|---|---|
| | | | | | | | | |
| | | | | | | | | |
| Subsystem Name: | | Resistance System | | | | | | |
| Requested by: | | Ray D, Blake P, Tyler C, Benjamin R, and Sage M | | | | | | |
| Approve by: | | | | | | | | |
| Total Cost: | | $427.48 | | | | | | |
| | | | | | | | | |
| | | | | | | | | |
| Level | Part # | Part Name | Supplier |  Supplier Part # | Qty |  Units | Unit Cost | Cost  |
| 1 | RS100 | Assembly | None | None |  1  |  Assy  | $0.00 |  $0.00  |
| 1.1 | ALUMPLATE100  | Aluminum Plate 10" X10"X 0.5" | Online Metals | 4535 |  1  |  Sheet | $70.32  |  $70.32 |
| 2 | HBRIDGE100 | Assembly | None | None |  1  |  Assy  | $0.00 |  $0.00  |
| 2.1 | SOCK100 | DC Connector -Male | TME | XT30PW-M |  1  |  Piece | $0.63 |  $0.63  |
| 2.2 | MOSFET100 | MOSFET | DIGIKEY | G26P04K |  2  |  Piece | $0.78 |  $1.56  |
| 2.3 | MOSFET101 | MOSFET | DIGIKEY | AOD424 |  2  |  Piece | $0.98 |  $1.96  |
| 2.4 | WIFIREC100 | Bluetooth Receiveer | ALIEXPRESS  | HC-06 |  1  |  Piece | $2.24 |  $2.24  |
| 2.5 | DIODE100 | Diode | DIGIKEY | B320-13-F |  4  |  Piece | $0.48 |  $1.92  |
| 2.6 | BJT100 | BJT | DIGIKEY | DDC114YU-7-F |  1  |  Piece | $0.43 |  $0.43  |
| 2.7 | CHRESIST100 | Chip Resistor | DIGIKEY | CRCW120610K0JNEA |  2  |  Piece | $0.10 |  $0.20  |
| 2.8 | CHRESIST101 | Chip Resistor | DIGIKEY | ERJ-8GEYJ102V  |  2  |  Piece | $0.14 |  $0.28  |
| 2.9 |  CARBRESIST100  | 1k Resistor | DIGIKEY |  CFR-25JB-52-1K  |  3  |  Piece | $0.01 |  $0.03  |
| 2.10 |  CARBRESIST101  | 2.2k Resistor | DIGIKEY |  CFR-25JR-52-2K2 |  1  |  Piece | $0.01 |  $0.01  |
| 2.11 | ARDNANO100 | Arduino Nano | Arduino | A000005 |  1  |  Piece | $24.90  |  $24.90 |
| 3 |  LINMOTORBRK100 | Assembly | None | None |  1  |  Assy  | $0.00 |  $0.00  |
| 3.1 | STLSH100 | 12" X 18" Steel sheet | Lowes | 44487 |  1  |  Stick | $9.48 |  $9.48  |
| 3.2 | STLROD100 | 3/8"X3' Steel Rod | Lowes | 44079 |  1  |  Stick | $7.48 |  $7.48  |
| 3.3 | BOLT100 | Bolt | Lowes | 61820 |  8  |  Piece | $0.15 |  $1.20  |
| 3.4 | WASH100 | Washer | Lowes | 63306 |  8  |  Piece | $0.15 |  $1.20  |
| 3.5 | NUT100 | Nut | Lowes | 63301 |  8  |  Piece | $0.10 |  $0.80  |
| 4 | LINMOTORASSY100 | Assembly | None | None |  1  |  Assy  | $0.00 |  $0.00  |
| 4.1 | LINMOTOR100 | Linear Motor | Pololu | GF23-120502-3-65 |  1  |  Piece |  $183.95  | $183.95 |
| 4.2 | MG100 | Magnet - 2" by 0.125" Thickness |  kjmagnetics  | DY04-N52 |  2  |  Piece | $28.44  |  $56.88 |
| 4.3 | ADH100 | Adhesive | Lowes | 50112 |  1  | Bottle | $7.98 |  $7.98  |
| 4.4 | STLFLTBAR100  | Flat Bar - Steel | Lowes | 216190 |  1  |  Stick | $12.98  |  $12.98 |
| 4.5 | BOLT100 | Bolt | Lowes | 61820 |  4  |  Piece | $0.15 |  $0.60  |
| 4.6 | WASH100 | Washer | Lowes | 63306 |  4  |  Piece | $0.15 |  $0.60  |
| 4.7 | NUT100 | Nut | Lowes | 63301 |  4  |  Piece | $0.10 |  $0.40  |
| 4.8 | LINMTRMNT100  | Linear Motor Mount | Pololu | 2328 |  1  | Set  | $39.45  |  $39.45 |
| | | | | | | | |  $0.00  |
| | | | | | | | |  $0.00  |
| | | | | | | | Total | $427.48 |

### References:

[1]	A. H. C. Gosline and V. Hayward, "Eddy Current Brakes for Haptic Interfaces: Design, 	Identification, and Control," in IEEE/ASME Transactions on Mechatronics, vol. 13, no. 	6, pp. 669-677, Dec. 2008, doi: 10.1109/TMECH.2008.2004623.

[2]	“How to Start an Exercise Program,” American Council on Exercise, vol. FF, 2013. 

[3]	R. Gregor and L. Childers, “4,” in Neuromechanics of the Cycling Task, Blackwell 	Publishing Ltd, 2011, pp. 52–77.

[4]	RC;, H. (1989, March). Contact pressures in the patellofemoral joint during impact loading on the human flexed knee. Journal of orthopaedic research: official publication of the Orthopaedic Research Society. Retrieved November 19, 2022, from https://pubmed.ncbi.nlm.nih.gov/2918426/

[5]	Magnetic Dipole Moment. [Online]. Available: https://www.kjmagnetics.cm/blog.asp?p=dipole.

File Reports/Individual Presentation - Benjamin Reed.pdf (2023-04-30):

# HDMI

# High-Definition Multimedia Interface

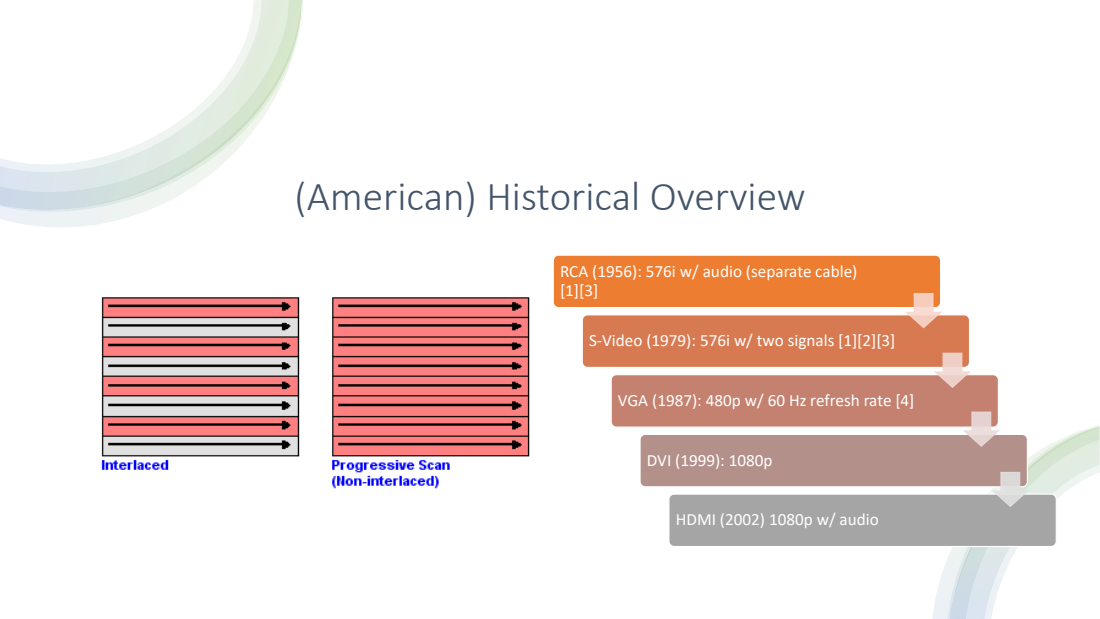
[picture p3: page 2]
DVI (1999): 1080p; HDMI (2002) 1080p w/ audio

(American) Historical Overview

RCA (1956): 576i w/ audio (separate cable)

S-Video (1979): 576i w/ two signals [1][2][3]

VGA (1987): 480p w/ 60 Hz refresh rate [4]

# Why HDMI?

# Quality

- 720p [4]
- 1080i

# - Uncompressed

# Simplicity

# - Built-in audio - Automatic aspect ratio detection - Eliminates wires and infrared repeaters - Remote controlled

# “Better Picture, Easier to Use”

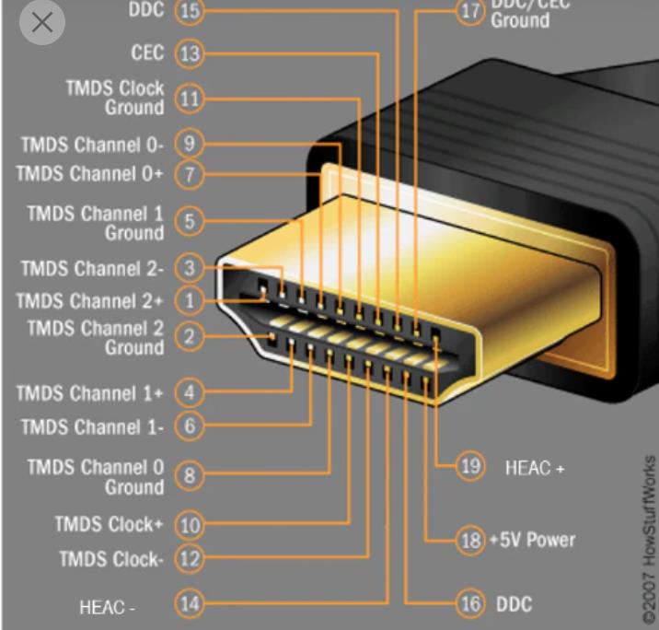
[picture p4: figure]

# HDMI Overview

## - Display Data Channel [5] - Consumer Electronics Control - HDMI Ethernet and Audio Return Channel - Transition-Minimized Differential Signaling - +5V Power Source

# Display Data Channel (DDC)

## - Protocol for extended display information data (EDID) [6] - Brand [7] - Product Code - Date of Manufacture - Video Input Type - Horizontal and Vertical Size - Supported features - Color characteristics - Timing information

# Consumer Electronics Control

(CEC) | Example: Controlling a Blu-Ray with a TV
| Remote

# User control over connected devices [8]

# Blu-Ray Media streamers

# Game consoles

# HDMI Ethernet and Audio Return Channel (HEAC)

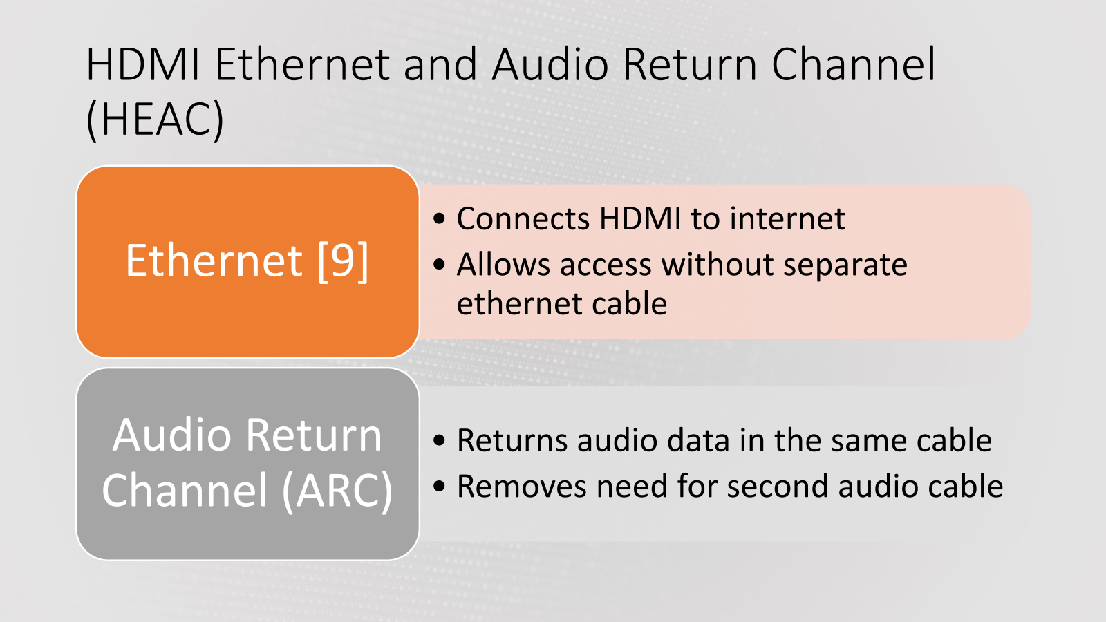
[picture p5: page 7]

# - Connects HDMI to internet - Allows access without separate ethernet cable

# Ethernet [9]

# - Returns audio data in the same cable - Removes need for second audio cable

# Audio Return Channel (ARC)

# Transition-Minimized Differential Signaling (TMDS)

# Why?

# •Interference [10] •Noise •Signal Loss

# Why not parity checking?

# •Faster transmissions •More transmissions

# TMDS Continued

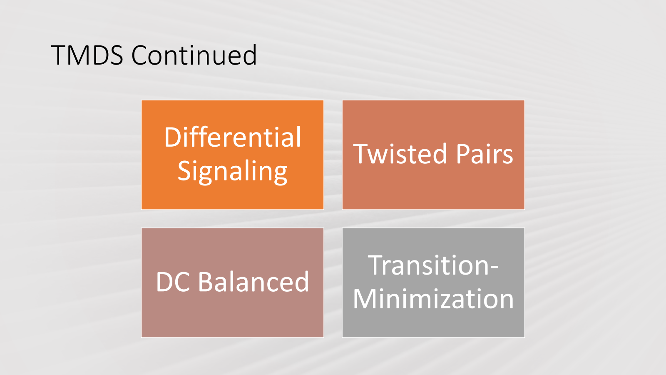
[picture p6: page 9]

# Differential

Signaling | Twisted Pairs
DC Balanced | Transition- Minimization

# References

- [1] | “Composite Video vs. S-Video.” diffen.com. https://www.diffen.com/difference/Composite_Video_vs_S-video
- [2] | G. Chidiogo, “S-Video Resolutions: A 101 Guide.” pointerclicker.com. https://pointerclicker.com/s-video- resolutions/#:~:text=S%2Dvideo%20input.- ,What%20is%20the%20Highest%20Resolution%20S%2DVideo%20Can%20Handle%3F,is%20limited%20in%20its%20performance. (accessed Mar. 7, 2023).
- [3] | N. Watkins, “History of Video Cables.” showmecables.com. https://www.showmecables.com/blog/post/history-of-video- cables (accessed Mar. 7, 2023).
- [4] | The HDMI Working Group, “HDMI.” web.archive.org. https://web.archive.org/web/20160106223845/http://www.hdmi.org/pdf/HDMI_CPTWG_4-17-02.PDF (accessed Mar. 7, 2023).
- [5] | T. V. Wilson, “How HDMI Works.” howstuffworks.com, https://electronics.howstuffworks.com/hdmi.htm (accessed Mar. 7, 2023).
- [6] | “DDC (Display Data Channel).” blackbox.be. https://www.blackbox.be/ben-be/page/25829/Resources/Technical-Resources/Black-Box- Explains/multimedia/ddc-display-data-channel (accessed Mar. 7, 2023).
- [7] | “What is EDID? (Extended Display Identification Data).” cie-group.com. https://cie-group.com/how-to-av/videos-and-blogs/what-is-edid- extended-display-identification-data (accessed Mar. 7, 2023).
- [8] | “What is CEC? (Consumer Electronics Control).” cie-group.com. https://cie-group.com/how-to-av/videos-and-blogs/what-is-cec-consumer- electronics-control (accessed Mar. 7, 2023).
- [9] | G. Morrison, “HDMI ARC and eARC: Audio Return Channel for Beginners.” cnet.com. https://www.cnet.com/tech/home- entertainment/hdmi-audio-return-channel-and-earc-for-beginners/ (accessed Mar. 7, 2023).
- [10] | “What’s a TMDS and Why is it in my HDMI?” ramoem.com. https://www.ramoem.com/tmds.html (accessed Mar. 7, 2023).

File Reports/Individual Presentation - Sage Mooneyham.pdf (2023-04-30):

# Bluetooth Low Energy (BLE) Communication Process

by Sage Mooneyham

## Background

- Relatively new technology (introduced in 2010)
- Digital Radio Protocol
- Transmits via Radio Waves
- Designed for low power consumption, bandwidth, complexity
- Classic Bluetooth is not directly compatible with BLE

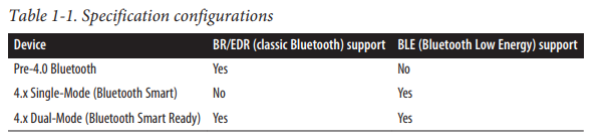
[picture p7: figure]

## BLE and the ISM Radio Band

- ISM: Industrial, Scientific, Medical
- Range of frequencies reserved for ISM purposes.
- Frequency ranges must be defined and allotted, as devices operating on the same/similar frequencies can interfere with each other
- BLE operates on the 2.4 GHz ISM band (2.4000 – 2.4835 GHz range)
- 40 channels of 2 MHz spacing (37 for connection, 3 for advertising)
- Operates in the same frequency as Bluetooth Classic and Wifi

## Frequency Hopping Spread Spectrum (FHSS)

- Method by which the carrier frequency hops to different channels in the range
- BLE uses FHSS to reduce potential interference and eavesdropping
- NextChannel = (CurrentChannel + Hop) % 37
- Hop is defined randomly at connection time between two devices
- These hops occur multiple times a second, sending data in bursts
- BLE goes a step further, using a variation of FHSS

## Adaptive Frequency Hopping (AFH)

- Works the same as Frequency Hopping Spread Spectrum
- Main device in connection creates a channel map
- Continuously updates status of channels and shares with connection

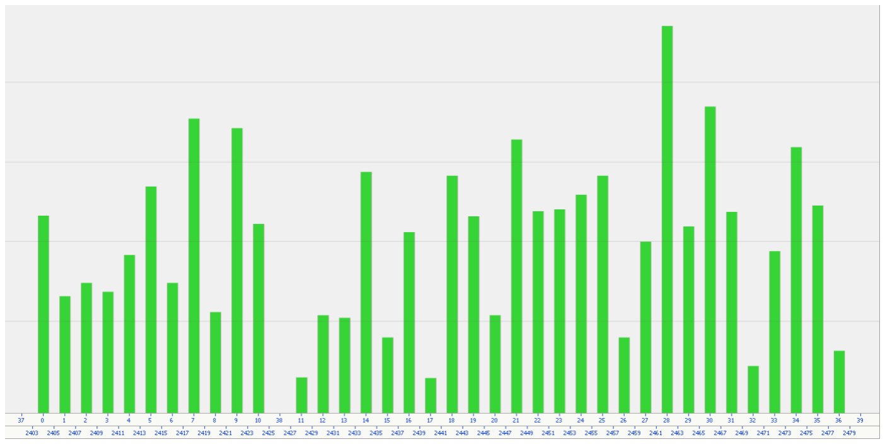
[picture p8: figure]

## BLE Packet Format (v4.2)

- Preamble: used for synchronization
- Access Address: Random value (distinguishes devices on same channel)
- PDU: Protocol Data Unit
- Differs based on channel type
- Header: formatting
- Payload: message being sent
- MIC: message integrity check
- CRC: Cyclic Redundancy Check

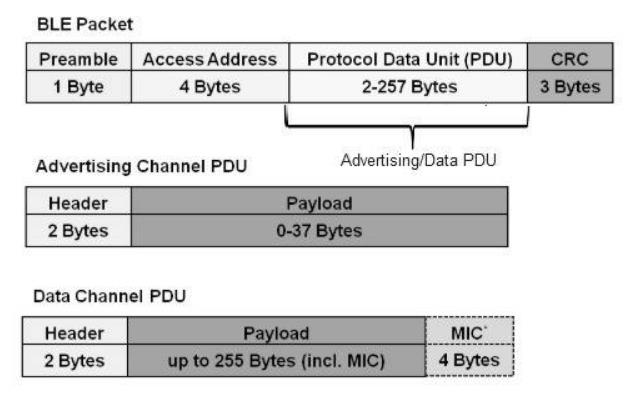
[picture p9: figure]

## Signal Modulation

- Generally, signals are low frequency, and need to be modulated (coded/packaged) in order to be properly transmitted.
- Especially important in long range wireless communication
- Amplitude, Frequency, and Phase Modulation
- BLE uses a variation of Frequency Modulation
- Gaussian Frequency Shift Keying (GFSK)

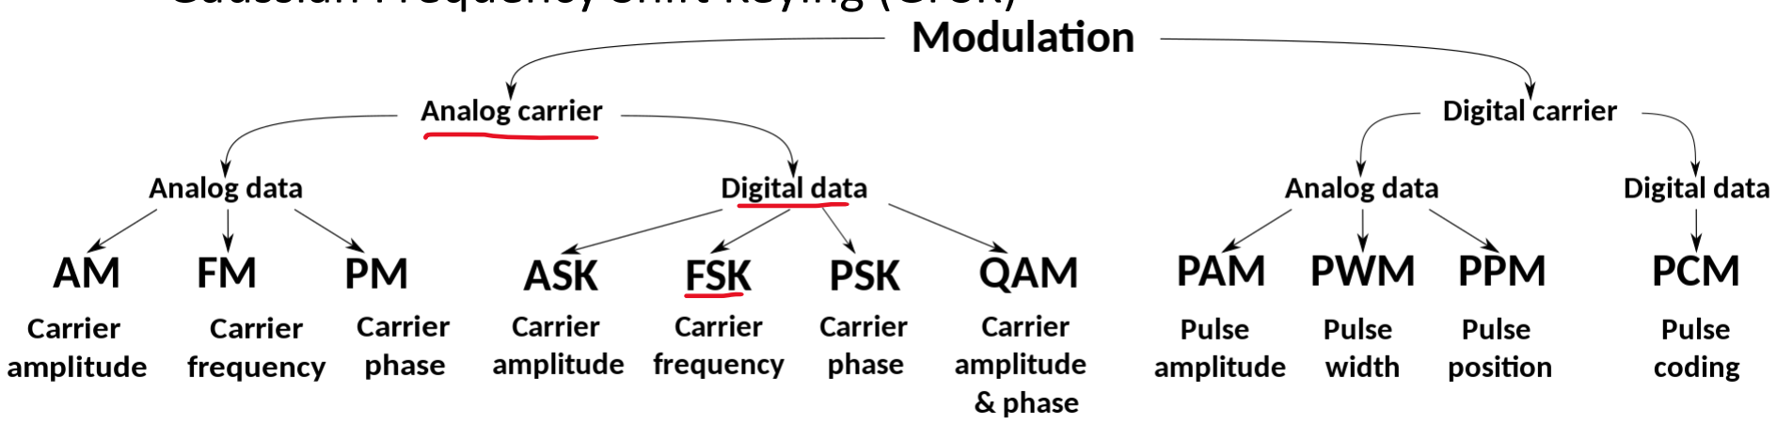
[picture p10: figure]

## Frequency Shift Keying

- In FSK, frequency of the carrier signal is shifted(changed) to multiple discrete frequencies based on the digital signal

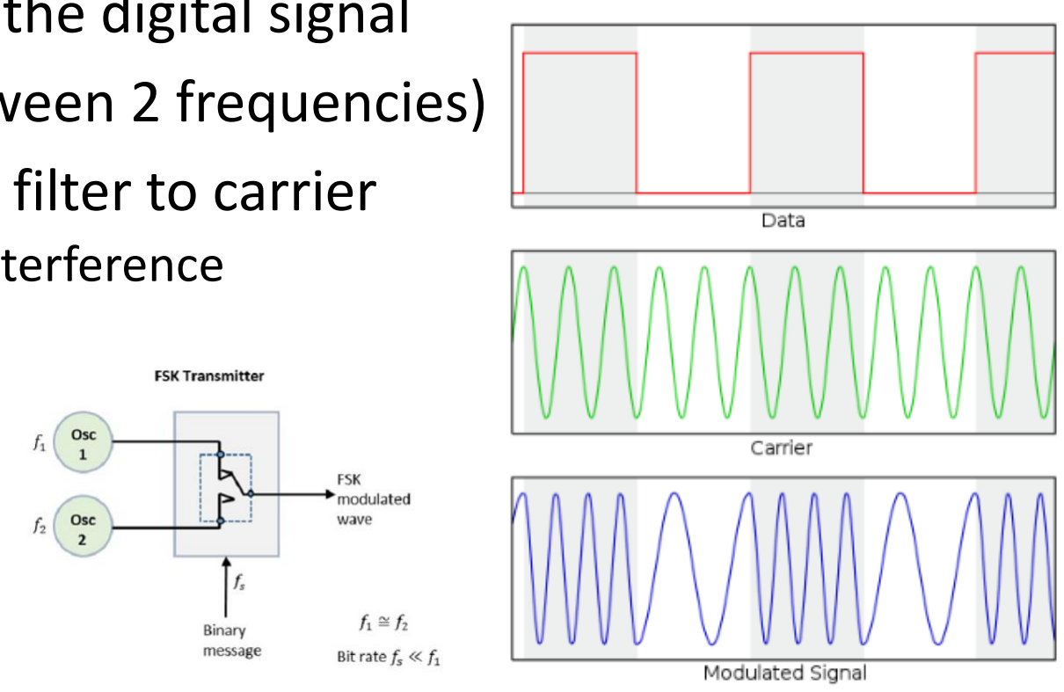
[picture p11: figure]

- Binary FSK is used (switch between 2 frequencies)
- Gaussian FSK applies Gaussian filter to carrier
- Reduces sideband power and interference
- Data Throughput: 1 Mbps

## Synchronous Demodulation

- Data must be demodulated (unpacked) when at receiver.
- Performed through the use of two bandpass filters and envelope detectors
- Envelope detectors take the shape of the peak of a signal, and return the original shape of the intended message
- From here, a decision circuit compares the inputs, and chooses which input is most likely the original message

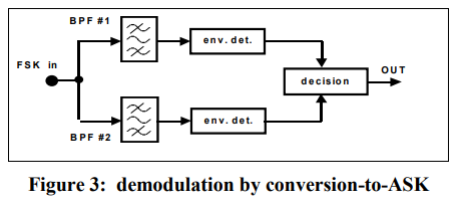
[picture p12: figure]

## Sources

- https://en.wikipedia.org/wiki/Bluetooth_Low_Energy#:~:text=Bluetooth%20Low%20Energy%20t echnology%20operates,has%2040%202%2DMHz%20channels. (https://en.wikipedia.org/wiki/Bluetooth_Low_Energy)
- https://www.bluetooth.com/blog/how-bluetooth-technology-uses-adaptive-frequency-hoppingto-overcome-packet-interference/ (https://www.bluetooth.com/blog/how-bluetooth-technology-uses-adaptive-frequency-hopping-to-overcome-packet-interference/)
- https://en.wikipedia.org/wiki/Frequency-shift_keying
- https://www.tutorialspoint.com/digital_communication/digital_communication_frequency_shift_keying.htm (https://www.tutorialspoint.com/digital_communication/digital_communication_frequency_shift_keying.htm)
- https://www.eng.auburn.edu/~troppel/courses/TIMS-manualsr5/TIMS%20Experiment%20Manuals/Student_Text/Vol-D1/D1-07.pdf

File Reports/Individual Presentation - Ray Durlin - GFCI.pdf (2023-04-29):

# Ground Fault Circuit Interruption (GFCI)

Presented by: Ray Durlin

## What is a Ground Fault?

- Any unplanned and non-restricted flow of charge to
ground
- A ground fault is defined by the National Electric Code as an unintentional conductive
connection between an
ungrounded conductor and
ground or a normally non-current carrying conductor
- Non-current carrying conductor include personnel or equipment

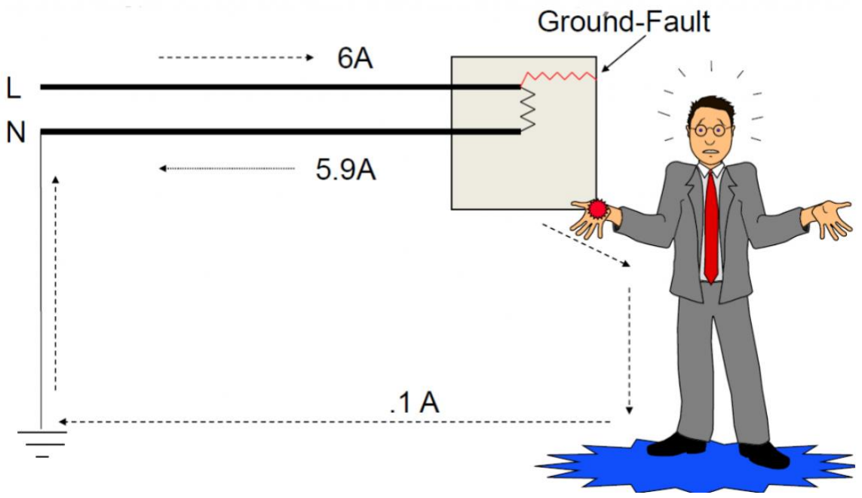
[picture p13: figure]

## Example of a Ground Fault?

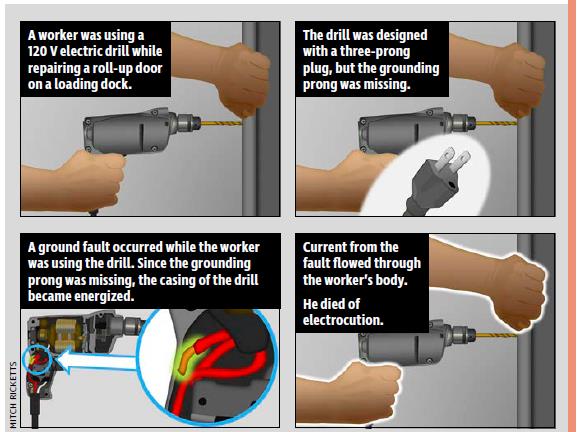
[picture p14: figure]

- Worker was using a 120 VAC drill
to complete a repair
- Drill was missing the ground prong on the power cable
- Ground fault occurred inside of the drill causing the drill casing to become energized
- Worker died of electrocution

## Why is Ground Fault Protection Important?

- Electric shock claims about 300
lives and causes thousands of
nonfatal injuries per year
- Ground faults are among one of the leading causes of electrical injuries
- Sources of electric shock vary from high voltage power lines to household appliances such as a coffee maker
- Electrical fires to homes and equipment are another hazard that is causes by ground faults

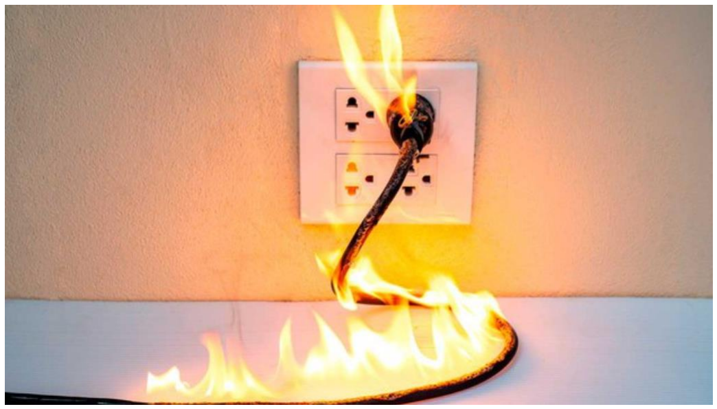
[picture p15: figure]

## Ground Fault Pathways

- Series Ground Fault
- When a person is the only pathway current to ground
- Example
- Ground fault occurs on a piece of equipment that requires a 3-wire prong plug, but the operator uses a 2 to 3 wire adapter, and does not properly ground the ground wire to the outlet plate
- A person operating this equipment and the equipment has a ground fault that energizes the equipment case
- Parallel Ground Fault
- Path to ground and person is in parallel
- Example
- Equipment is grounded, but no GFCI in place
- Equipment experiences a ground fault, and the operator is touching a ground such as a metal pipe
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

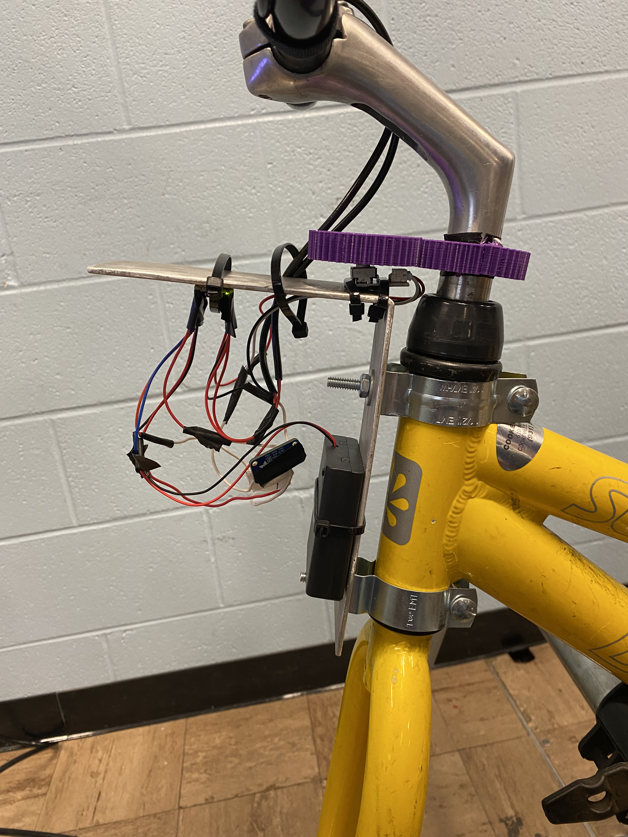
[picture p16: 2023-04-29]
Documentation/Images/L-Bracket.jpg

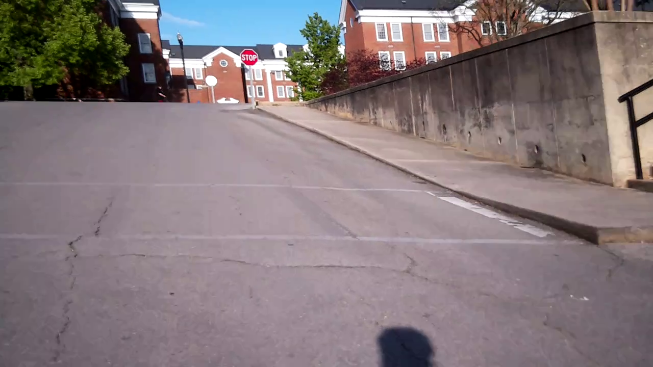
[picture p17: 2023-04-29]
Documentation/Images/RRSA Footage Example.png

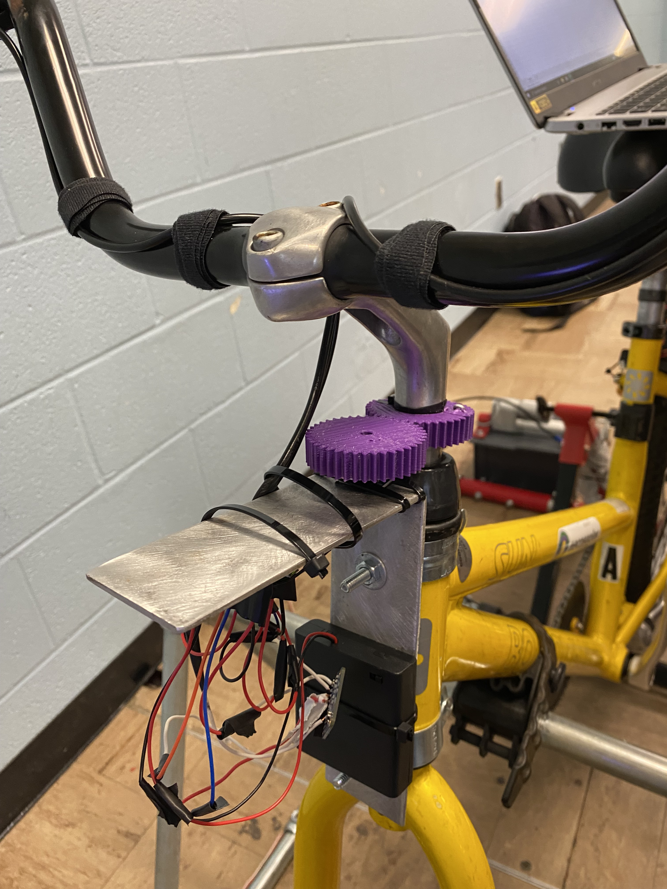
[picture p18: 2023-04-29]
Documentation/Images/L-Bracket 2.jpg

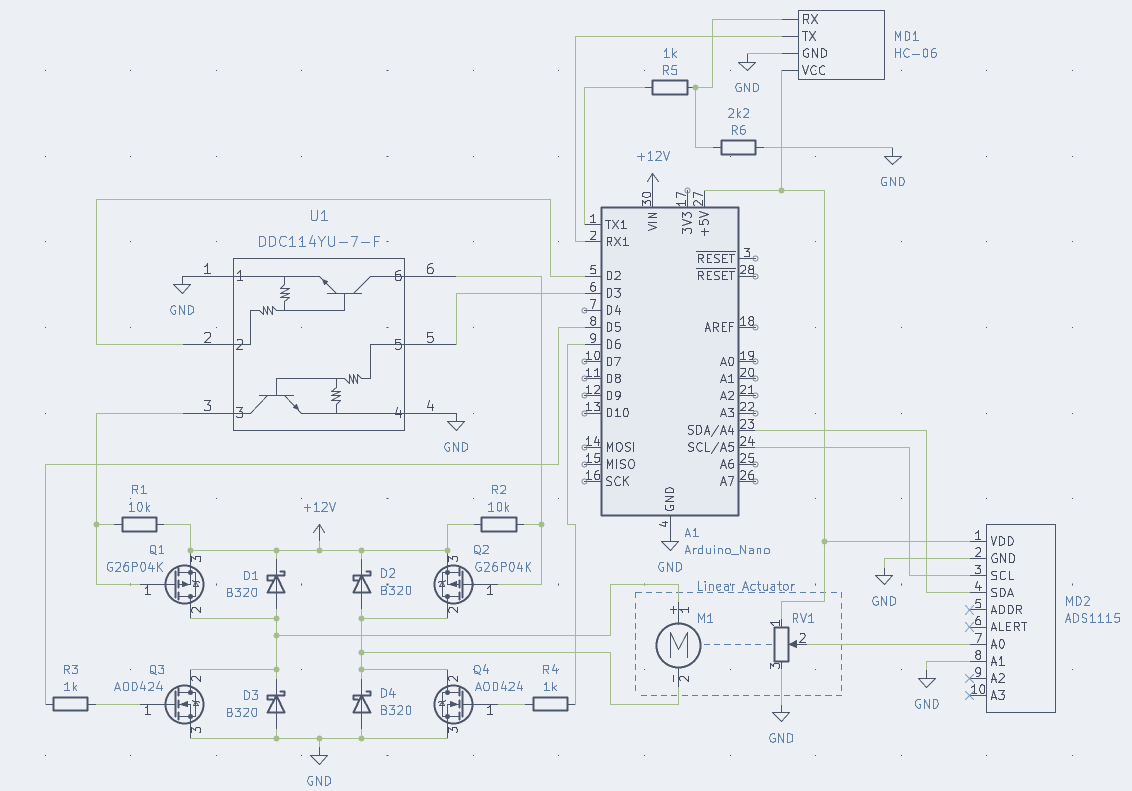
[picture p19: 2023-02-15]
Documentation/Electrical/Ride Resistance System Control Circuit.png

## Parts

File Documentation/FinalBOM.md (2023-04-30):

| Subsystem Name: | | Final Assembly | | | | | | |
|---|---|---|---|---|-----|---|---|---|
| Requested by: | | Ray D, Blake P, Tyler C, Sage M, Ben R | | | | | | |
| Approve by: | | | | | | | | |
| Total Cost: | | | | | | | | |
| | | | | | | | | |
| | | | | | | | | |
| Level | Part # | Part Name | Supplier | Supplier Part # | Qty | Units | Unit Cost | Cost |
| 1 | Power Distribution Subsystem | | | | | | | |
| 1.1 | ENCL1 | BOX STEEL GRAY 12"L X 12"W | Digikey | CS12126 | 1 | ea. | $39.65 | $39.65 |
| 1.2 | CBLCLMP-5 | 5-Pack Cable Clamp | Lowes | 75637 | 1 | ea. | $4.34 | $4.34 |
| 1.3 | PLXGLS2 | 11 in. x 14 in. x .093 in. Acrylic Sheet | Amazon | B0BHHJ2XSF | 1 | ea. | $8.28 | $8.28 |
| 1.4 | DINRAIL | TS35 Din Rail 35mm x 7.5mm | DigiKey | ADR3575-U7874-ND | 1 | ea. | $7.06 | $7.06 |
| 1.5 | EPDM | EPDM 1/8 in. x 36 in. x 96 in. Commercial Grade 60A Rubber Sheet | Home Depot | 303371976 | 1 | ea. | $0.00 | $0.00 |
| 1.6 | PS1 | 120 VAC / 5 VDC Power Supply | DigiKey | 102-PSK-45-5-DIN-ND | 1 | ea. | $22.65 | $22.65 |
| 1.7 | PS2 | 120 VAC/ 12 VDC Power Supply | Mouser | 490-PSK-60-12-DIN | 1 | ea. | $24.93 | $24.93 |
| 1.8 | PS3 | 120 VAC / 15 VDC Power Supply | DigiKey | 102-PSK-45-15-DIN-ND | 1 | ea. | $22.65 | $22.65 |
| 1.9 | SWTCH | 20 A Toggle Switch | Lowes | 76457 | 1 | ea. | $15.89 | $15.89 |
| 1.10 | 14GACONN | 16 - 14 AWG #8 - 10 Stud Size Vinyl-Insulated Spade Terminals, Blue (15-Pack) | Home Depot | 202522889 | 1 | ea. | $3.63 | $3.63 |
| 1.11 | CB-3A | CIRCUIT BREAKER 3A | DigiKey | 277-17752-ND | 3 | ea. | $19.00 | $57.00 |
| 1.12 | 14WIRE | 25 ft. 14 Black Solid CU THHN Wire | Home Depot | 301210609 | 1 | ea. | $0.00 | $0.00 |
| 1.13 | 14WIRERED | 25 ft. 14 Red Solid CU THHN Wire | Home Depot | 1000129222 | 1 | ea. | $0.00 | $0.00 |
| 1.14 | 14WIREWHITE | 25 ft. 14 White Solid CU THHN Wire | Home Depot | 1000129222 | 1 | ea. | $0.00 | $0.00 |
| 1.15 | 14WIREGREEN | 25 ft. 14 Green Solid CU THHN Wire | Home Depot | 1000129222 | 1 | ea. | $0.00 | $0.00 |
| 1.16 | GRDBAR | 4 Terminal Grounding Bar | Home Depot | 100207842 | 1 | ea. | $8.31 | $8.31 |
| 1.17 | GFCI-15 | 15 Amp Compact Right Angle Plug-In GFCI, Black | Home Depot | 205189963 | 1 | ea. | $21.99 | $21.99 |
| 1.18 | WARNLAB | 120 VAC Warning Label | None | None | 1 | ea. | $0.00 | $0.00 |
| 1.19 | TRMBLK | Terminal Block | DigiKey | 277-2026-ND | 10  | ea. | $1.53 | $15.30 |
| 1.20 | TRMJMP | 3 Pos - Terminal Block Jumper | DigiKey | 277-3230-ND | 3 | ea. | $1.80 | $5.40 |
| 1.21 | CONN1 | Linear Motor Control Connector | TME | XT30U-F | 1 | ea. | $0.45 | $0.45 |
| 1.22 | CBMAIN-1 | CIRCUIT BREAKER 15A | Digikey | 277-17761-ND | 1 | ea. | $19.00 | $19.00 |
| 1.23 | TERMSTP4 | 4 Lug Terminal Strip | DigiKey | A98505-ND | 4 | ea. | $2.94 | $11.76 |
| 1.24 | VHBTAPE | VHB Double Sided Tape | Amazon | B01BU7038A | 1 | ea. | $0.00 | $0.00 |
| 1.25 | POWERCORD | 10 Ft Power Cord | Home Depot | 1004154266 | 1 | ea. | $0.00 | $0.00 |
| 2 | Linear Actuator Assembly | | | | | | | |
| 2.1 | LINMOTOR100 | Linear Motor | Pololu | 4953 | 1 | ea. | $183.95 | $183.95 |
| 2.2 | SCR3 | #3 x 1/2 in. Phillips Head Brass Wood Screw (6-Pack) | Home Dept | 204587520 | 1 | bag | $1.38 | $1.38 |
| 2.3 | PLXGLS | 20 in. x 32 in. x 0.093 in. Acrylic Sheet | Home Dept | 202038049 | 1 | ea. | $25.48 | $25.48 |
| 2.4 | CBLCLMP1 | CBL CLAMP P-TYPE BLACK FASTENER | DIGIKEY | N-32B-BK | 2 | ea. | $1.20 | $2.40 |
| 2.5 | 14WIRE | 25 ft. 14 Black Solid CU THHN Wire | Home Depot | 301210609 | 1 | ea. | $0.00 | $0.00 |
| 2.6 | 14GACONN | 16 - 14 AWG #8 - 10 Stud Size Vinyl-Insulated Spade Terminals, Blue (15-Pack) | Home Depot | 202522889 | 1 | ea. | $3.63 | $3.63 |
| 2.7 | SCR2 | #2 x 1/4 in. Phillips Flat Head Zinc Plated Wood Screw (8-Pack) | Home Dept | 204587381 | 4 | bag | $1.38 | $5.52 |
| 2.8 | LNMTCLP | Routing Clamp | McMaster Carr | 3039T16 | 3 | ea. | $2.92 | $8.76 |
| 2.9 | BRKPLT | 12 in. x 12 in. 22-Gauge Weldable Sheet | Home Dept | 100237896 | 1 | ea. | $13.57 | $13.57 |
| 2.10 | AXLMNT | 10mm Universal Aluminum Mounting Hubs for Shaft – 18009 | OzRobitics | 18009 | 1 | ea. | $9.40 | $9.40 |
| 2.11 | SELFTAPESCREW | #7Self Taping Screw | Lowes | 916579 | 1 | ea. | $0.00 | $0.00 |
| 3 | Steering L-Bracket | | | | | | | |
| 3.1 | BKTM02X12X07HSCRS | 12-in x 2-in x 7-in Stainless Steel Support Bracket | Lowe’s | 1647965 | 1 | ea. | $19.68 | $19.68 |
| 3.2 | 49120 | 1-in Steel Conduit Hangers | Lowe’s | 63200 | 2 | ea. | $0.98 | $1.96 |
| 3.3 | 490435 | 1/4-in- 20 x 1-in Phillips-Drive Machine Screws | Lowe’s | 58050 | 1 | bag | $1.38 | $1.38 |
| 4 | Wireless Sensor Subsystem | | | | | | | |
| 4.1 | 4AA-Switch-2P-A | 4 AA Battery Holders | Amazon | B07L9M6VZK | 1 | ea. | $7.49 | $7.49 |
| 4.2 | L91 | 24 Pack AA Lithium Batteries | Amazon | B01C4PP8FK | 1 | ea. | $65.79 | $65.79 |
| 4.3 | MIC94053YC6-TR | MOSFET P-CH 6V 2A SC70-6 | DIGIKEY | 576-2939-2-ND - Tape & Reel (TR) | 1 | ea. | $0.74 | $0.74 |
| 4.4 | TXLAC | 8 Inch Zip Ties | Amazon | B07TG9VMWY | 1 | ea. | $4.49 | $4.49 |
| 4.5 | 300876 | Electrical Tape | Amazon | B002VKT22O | 1 | ea. | $5.49 | $5.49 |
| 4.6 | ABX00030 | Nano 33 BLE | Amazon | ‎B07WV59YTZ | 2 | ea. | $29.49 | $58.98 |
| 5 | HDMI Switcher Assembly | | | | | | | |
| 5.1 | BHS100 | HDMI Switcher | Amazon | N/A | 1 | ea. | $10.99 | $10.99 |
| 5.2 | RELAY100 | TXS2-L-3V Relay | DIGIKEY | 255-1899-ND | 1 | ea. | $5.30 | $5.30 |
| 5.3 | DIODE100 | 1N5818 Diode | DIGIKEY | 497-4548-1-ND | 1 | ea. | $0.40 | $0.40 |
| 6 | Resistance System Control Circuit | | | | | | | |
| 6.1 | SOCK100 | AMASS XT30 DC Connector - Male | TME | XT30PW-M | 1 | ea. | $0.63 | $0.63 |
| 6.2 | MOSFET100 | G26P04K P-Channel MOSFET | Digikey | 3141-G26P04KCT-ND | 1 | ea. | $0.78 | $0.78 |
| 6.3 | MOSFET101 | AOD424 N-Channel MOSFET | Digikey | 785-1565-1-ND | 2 | ea. | $0.98 | $1.96 |
| 6.4 | WIFIREC100 | HC-06 Bluetooth Transceiver | Amazon | ‎B074J5WMH1 | 2 | ea. | $2.24 | $4.48 |
| 6.5 | SOCK200 | Socket Header for Transceiver | Digikey | 2057-SMC-1-04-1-GT-ND | 1 | ea. | $0.33 | $0.33 |
| 6.6 | DIODE100 | B320 Schottky Diode | Digikey | B320-FDICT-ND | 1 | ea. | $0.48 | $0.48 |
| 6.7 | BJT100 | DDC114YU-7-F Dual Pre-biased BJT (NPN) | Digikey | DDC114YU-FDICT-ND | 4 | ea. | $0.43 | $1.72 |
| 6.8 | CHRESIST100 | CRCW120610K0JNEA 10k Chip Resistor | Digikey | 541-10KECT-ND | 1 | ea. | $0.10 | $0.10 |
| 6.9 | CHRESIST101 | ERJ-8GEYJ102V 1k Chip Resistor | Digikey | P1.0KECT-ND | 2 | ea. | $0.14 | $0.28 |
| 6.10 | CARBRESIST100 | CFR-25JB-52-1K 1k THT Resistor | Digikey | 1.0KQBK-ND | 2 | ea. | $0.10 | $0.20 |
| 6.11 | CARBRESIST101 | CFR-25JB-52-2K2 2.2k THT Resistor | Digikey | 2.2KQBK-ND | 3 | ea. | $0.10 | $0.30 |
| 6.12 | ARDNANO100 | Arduino Nano Microcontroller | Arduino | A000005 | 1 | ea. | $24.90 | $24.90 |
| 6.13 | SOCK300 | Socket Header for Arduino | Digikey | 2553-2042-1X15G00SA-ND | 1 | ea. | $0.74 | $0.74 |
| 6.14 | ADC100 | ADS1115 4-Channel 16-Bit ADC Module | Protosupplies | MOD-83 | 2 | ea. | $5.95 | $11.90 |
| 6.15 | SOCK400 | Socket Header for ADC Modele | Digikey | ED5864-10-ND | 1 | ea. | $2.52 | $2.52 |
| 6.16 | PCB100 | Printed Circuit Board for Controller Circuit | JLCPCB | Y10-4812191A | 1 | ea. | $9.50 | $9.50 |
| 7 | Ride Resistance System Data Acquisition | | | | | | | |
| 7.1 | COMP1 | Raspberry Pi 3 Model B | The Pi Hut | SC0050 | 1 | ea. | $40.00 | $40.00 |
| 7.2 | MEM1 | 128 GB Micro SD Card | Newegg | N82E16820215186 | 1 | ea. | $9.49 | $9.49 |
| 7.3 | PSU1 | Raspberry Pi UPS HAT | DFRobot | DFR0528 | 1 | ea. | $16.20 | $16.20 |
| 7.4 | CABLE1 | AK67421-0.3-VM | Digikey | AE11229-ND | 2 | ea. | $2.58 | $5.16 |
| 7.5 | JACK1 | USB C Jack to USB A Jack Adapter | Adafruit | 4259 | 1 | ea. | $5.95 | $5.95 |
| 7.6 | SW1 | Rugged Metal On/Off Switch (Green LED) | Adafruit | 482 | 1 | ea. | $4.95 | $4.95 |
| 7.7 | SW3 | Rugged Metal Pushbutton (Red LED) | Adafruit | 559 | 1 | ea. | $4.95 | $4.95 |
| 7.8 | BT1 | Lithium Ion Battery Pack - 3.7V 6600mAh | Adafruit | 353 | 1 | ea. | $24.50 | $24.50 |
| 7.9 | SW2 | Hamlin SPST - N.O. Reed Switch | Electronics Goldmine | G26522 | 1 | ea. | $2.49 | $2.49 |
| 7.10 | ZT1 | Amazon Basics Multi-Purpose Cable Ties | Amazon | DS-SZS-002 | 1 | 200 pk. | $4.96 | $4.96 |
| 7.11 | MAG1 | Bike Wheel Magnet | Amazon | B000OYFENU | 1 | ea. | $6.95 | $6.95 |
| 7.12 | ALTSENSE1 | Adafruit DPS310 Module | Adafruit | 4494 | 1 | ea. | $6.95 | $6.95 |
| 7.13 | BOX1 | 220x170x110mm Junction Box | Amazon | B087F9TS25 | 1 | ea. | $29.99 | $29.99 |
| 7.14 | MNT1 | Bike Phone Mount | Amazon | B08R5K29BC | 1 | ea. | $19.99 | $19.99 |
| 7.15 | FASTENER1 | M2.5-0.45 x 10 mm Steel Machine Screws | Accu-Components | SIP-M2.5-8-A2 | 14  | ea. | $0.19 | $2.66 |
| 7.16 | FASTENER2 | M2.5-0.45 Zinc-Plated Metric Hex Nut | Accu-Components |  HPN-M2.5-A2 | 18  | ea. | $0.14 | $2.52 |
| 7.17 | FASTENER3 | Gorilla Max Strength Clear Adhesive | Amazon | B0916KZ598 | 1 | ea. | $7.96 | $7.96 |
| 7.18 | CAM1 | Camera Module for Raspberry Pi | DFRobot | SEN0173 | 1 | ea. | $24.90 | $24.90 |
| 7.19 | WIRE1 | Red Hookup Wire, 15', 22AWG | Electronics Goldmine | G26134 | 1 | ea. | $3.49 | $3.49 |
| 7.20 | WIRE2 | Black Hookup Wire, 15', 22AWG | Electronics Goldmine | G26138 | 1 | ea. | $3.49 | $3.49 |
| 8 | Resistance System | | | | | | | |
| 8.1 | ALUMPLATE100 | Aluminum Plate 10" X10"X 0.5" | Online Metals | 1250 | 1 | Sheet | $70.32 | $70.32 |
| 8.2 | MG100 |  Magnet - 2" by 0.125" Thickness | kjmagnetics | DY04-N52 | 2 | Piece | $28.44 | $56.88 |
| | | | | Total | 149 | | Total | $1,140.64 |

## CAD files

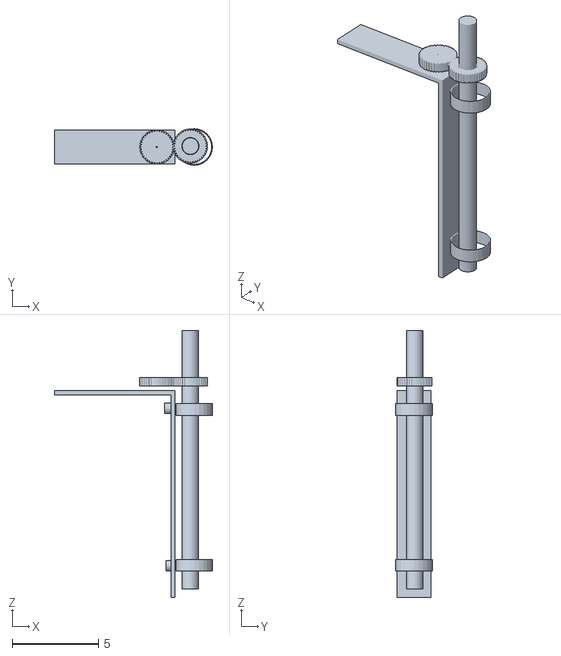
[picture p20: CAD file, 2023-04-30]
Documentation/3D Models/LBracket.stl
9.16 x 2.12 x 15.5

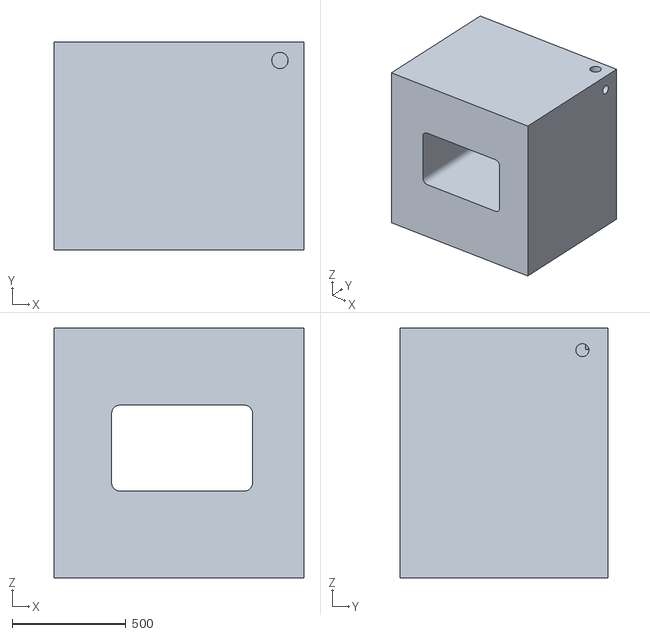
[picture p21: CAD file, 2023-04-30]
Documentation/3D Models/EnclosureDWG.stl
1097.0 x 914.2 x 1097.0

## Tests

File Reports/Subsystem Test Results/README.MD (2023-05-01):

This folder contains test data for the RRS Control and RRSA subsystems. It also contains some of our collected rumble data, which may prove useful to anyone attempting to make sense of the runble data outputs from the Nintendo Switch.

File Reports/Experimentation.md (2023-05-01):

### Team 4 – Mario Kart & Ride Replay Simulator

### Team Members: Ray Durlin, Blake Pickett, Tyler Chittum, Benjamin Reed, and Sage Mooneyham
<br /><br />

### Experimentation
<br /><br />
**Resistance Subsystem**
<br />
| Item | Testing Criteria | Testing Method | Measure of Success (MOS) | MOS Met? | What is needed for Improvement? |
|---|---|---|---|---|---|
| Magnet Distance Range | A distance range of 2-25mm from magnet to flywheel was selected, as these distances matched up well with the torque values that we want the resistance system to apply. | Operate the linear actuator and measure the distance between the flywheel and magnets to ensure that a distance of 2 mm and 25 mm can be achieved | Operate the linear motor at a distance between 2 mm to 25 mm | Yes | Replace the linear actuator hub with a hub that will not move. Original hub that used screwed to tighten to the actuator shaft was not received |
| Minimum Tire Speed | The minimum speed of the bike tire shall be considered 116.35 rpm. This value is based on the American Council on Exercise's recommendation for the minimum speed required for moderate exercise on a bike [2]. This correlates to 2501.52 rpm in the flywheel. At speeds less than 116.35 rpm, the torque placed on the rider will not be specified to reach any minimum value, and the resulution of the resistance changes within this operating region is not specified. | Rotate the flywheel 2501 rpm to ensure that the magnets will be at it's furthest distance from the flywheel, thus not applying a specified torque or resistance to the user | Pedal the bike with a contonious 116.35 bike tire RPM | Yes | Minimum tire speed was achieved. After experimentation, it was found that the minimum tire speed should be decreased for optimum torque range |
| Maximum Tire Speed | The maximum speed of the bike tire shall be considered 288 rpm, a value that comes from the average pedaling rpm (118 rpm) of an elite level cyclist [3] (Wheel to pedal gear ratio = 2.444, so wheel speed = 2.444*pedal speed). This correlates to 6192 rpm in the flywheel due to the the rotational velocity ratio of 43:2 between the flywheel and the wheel. If the user passes this speed, no additional torque will be applied to avoid injury to rider. | Rotate the flywheel 6192 rpm to ensure that the magnets will be at it's furthest distance from the flywheel, thus not applying a any torque or resistance to the user | Pedal the bike with a contonious 288 bike tire RPM | No | Due to the size and balance of the flywheel, only 277 bike tire RPM was achieve. Improve upon the flywheel weight balance to allow for the bike to achieve 288 RPM continously |
| Maximum Torque at Minimum Speed | Using the value for tire minimum speed (116.35 rpm), we know that the maximum torque at this speed will be produced when the magnets are closest (2mm). From here, you can find magnetic field felt at the flywheel using equation 2. These values can be plugged into equation 1 to give the torque at the flywheel, which can then be converted to torque at the bike wheel/pedals using the gearing ratios between the components (this is explained in more detail later in the document). Using this logic, we find that the max torque at the minimum speed is 49.23 Nm. | Rotate the flywheel 2501 rpm to ensure that the magnets are 2 mm from the the flywheel. Ensure that the torque value is 49.23 N*m is achieved | Pedal the bike with a contonious 116.35 bike tire RPM and apply resistance to 49.23 Nm at the flywheel | No | Rider could not pedal the bike with more than 25 Nm of torque applied. Improvements include lowering the maximum torque required. |
| Minimum Torque at Minimum Speed | Using the above logic while setting magnet distance to the furthest value (25mm) and wheel speed to the minimum value, we find the minimum torque at minimum speed is 0.002 Nm. | Rotate the flywheel 2501 rpm to ensure that the magnets are 25 mm from the the flywheel. Ensure that the torque value is 0.002 N*m is achieved | Pedal the bike with a contonious 116.35 bike tire RPM and apply resistance to 0.002 Nm at the flywheel | No | Resistance at 25 mm while pedaling at 105 RPM is approx. 12.89 Nm. Improvements include adjusting the distance of the actuator by replacing with a longer shaft actuator. At its furthest distance of 90 mm the torque at the flywheel is 0.252 Nm (at 105 RPM) |
| Maximum Torque at Maximum Speed | Using the above logic while setting magnet distance to the closest value and wheel speed to the maximum value (288 rpm), we find the maximum torque at maximum speed is 121.85 Nm. Safety always being a concern, this force is much lower than what is needed to break any leg bone in the average person | Rotate the flywheel 6192 rpm to ensure that at a maximum torque value of 121.85 N*m is achieved | Pedal the bike with a contonious 288 bike tire RPM and apply resistance to 121.85 Nm at the flywheel | No | Improve upon experimental method and flywheel weight balancing to achieve measure of success |
| Minimum Torque at Maximum Speed | Using the above logic while setting magnet distance to the furthest value and wheel speed to the maximum value, we find the minimum torque at maximum speed is 0.004 N•m. | Rotate the flywheel 6192 rpm to ensure that the minimum torque value of 0.004 N*m is achieved | Pedal the bike with a contonious 288 bike tire RPM and apply resistance to 0.004 Nm at the flywheel | No | Replace the linear actuator to include a longer shaft. At its furthest position of 90 mm the torque on the flywheel is approximately 0.992 Nm |

<br /><br />

**Resistance Subsystem Data Analysis**
<br /><br />
*Data Gathered During Experiment*
<br /><br />

The bike was pedaled at a constant speed of either 105 RPM or 277 RPM of the bike tire. The magnet was positioned at a measured distance and recorded. The rider stopped 
pedaling the bike, and the time was recorded until the bike tire came to a complete stop. The acceleration was determined using the change in speed divided by the change in 
time. Using the formula torque equals mass multiplied by acceleration, the torque values were determined.

Figure 1 below represents the plot of torque values as seen by the riding using the gear ratio between the front and rear sprocket. The plots were created using the equation 
fit for each speed. The distance was limited to 0 to 60 mm as it best represented the raw data gathered. Figure 2 and 3 below represents the raw data gathered, which shows 
the smallest distance between the flywheel and the magnets that could be tested is 13 mm at 105 RPM and 14 mm at 277 RPM.

The plot validates initial experimentation that showed a lower amount of available torque at 277 RPM. This was an unexpected result and will need to be further investigated. 
Theoretically, the torque should be greater at a faster angular velocity. Possible causes for the inaccuracy are speculates that the flywheel mass or unbalancing may play a 
role in data accuracy. The root cause of the inaccuracy was not determined in this experimentation.

<br /><br />


<br />
Figure 1. Torque Vs. Distance at 105 RPM and 277 RPM Based on Trendline.

<br /><br />


<br />
Figure 2. Torque Vs. Distance at 105 RPM Raw Data.
<br /><br />


<br />
Figure 3. Torque Vs. Distance at 277 RPM Raw Data.

<br /><br />

Data Collected at 105 RPM
<br />
| Distance (mm) | Time (s) | Delta Velocity (m/s) | Acceleration (m/s^2) | Force (N) | Torque (Nm) on Tire | Torque on Pedal (N) |
|---|---|---|---|---|---|---|
| 90 | 8.46 | 3.212 | 0.380 | 0.861 | 0.252 | 5.407 |
| 85 | 7.42 | 3.212 | 0.433 | 0.982 | 0.287 | 6.165 |
| 82 | 7.17 | 3.212 | 0.448 | 1.016 | 0.297 | 6.380 |
| 77 | 6.9 | 3.212 | 0.465 | 1.056 | 0.308 | 6.630 |
| 73 | 6.73 | 3.212 | 0.477 | 1.082 | 0.316 | 6.797 |
| 70 | 6.58 | 3.212 | 0.488 | 1.107 | 0.323 | 6.952 |
| 65 | 6.6 | 3.212 | 0.487 | 1.104 | 0.322 | 6.931 |
| 61 | 6.45 | 3.212 | 0.498 | 1.129 | 0.330 | 7.092 |
| 57 | 5.6 | 3.212 | 0.574 | 1.301 | 0.380 | 8.169 |
| 54 | 5.75 | 3.212 | 0.559 | 1.267 | 0.370 | 7.956 |
| 50 | 5.06 | 3.212 | 0.635 | 1.440 | 0.420 | 9.041 |
| 46 | 6.16 | 3.212 | 0.521 | 1.183 | 0.345 | 7.426 |
| 40 | 5.63 | 3.212 | 0.570 | 1.294 | 0.378 | 8.125 |
| 38 | 5.02 | 3.212 | 0.640 | 1.451 | 0.424 | 9.113 |
| 35 | 4.25 | 3.212 | 0.756 | 1.714 | 0.501 | 10.764 |
| 31 | 3.94 | 3.212 | 0.815 | 1.849 | 0.540 | 11.611 |
| 28 | 3.74 | 3.212 | 0.859 | 1.948 | 0.569 | 12.232 |
| 25 | 3.55 | 3.212 | 0.905 | 2.052 | 0.599 | 12.886 |
| 20 | 3.29 | 3.212 | 0.976 | 2.214 | 0.647 | 13.905 |
| 17 | 2.59 | 3.212 | 1.240 | 2.812 | 0.822 | 17.663 |
| 13 | 1.85 | 3.212 | 1.736 | 3.937 | 1.150 | 24.728 |

<br /><br />

Data Collected at 277 RPM
<br />
| Distance (mm) | Delta Time (s) | Delta Velocity (m/s) | Acceleration (m/s^2) | Force (N) | Torque (Nm) on Tire | Torque on Pedal (N) |
|---|---|---|---|---|---|---|
| 90 | 16.18 | 8.473 | 0.524 | 1.188 | 0.347 | 7.459 |
| 83 | 16.33 | 8.473 | 0.519 | 1.177 | 0.344 | 7.390 |
| 80 | 16 | 8.473 | 0.530 | 1.201 | 0.351 | 7.543 |
| 76 | 18 | 8.473 | 0.471 | 1.068 | 0.312 | 6.705 |
| 71 | 16.9 | 8.473 | 0.501 | 1.137 | 0.332 | 7.141 |
| 67 | 17.01 | 8.473 | 0.498 | 1.130 | 0.330 | 7.095 |
| 64 | 17.05 | 8.473 | 0.497 | 1.127 | 0.329 | 7.078 |
| 59 | 16.43 | 8.473 | 0.516 | 1.170 | 0.342 | 7.345 |
| 56 | 16.12 | 8.473 | 0.526 | 1.192 | 0.348 | 7.487 |
| 51 | 16.23 | 8.473 | 0.522 | 1.184 | 0.346 | 7.436 |
| 46 | 15.88 | 8.473 | 0.534 | 1.210 | 0.353 | 7.600 |
| 44 | 15.9 | 8.473 | 0.533 | 1.209 | 0.353 | 7.590 |
| 40 | 15 | 8.473 | 0.565 | 1.281 | 0.374 | 8.046 |
| 37 | 15.7 | 8.473 | 0.540 | 1.224 | 0.358 | 7.687 |
| 32 | 14 | 8.473 | 0.605 | 1.373 | 0.401 | 8.620 |
| 27 | 11.3 | 8.473 | 0.750 | 1.701 | 0.497 | 10.680 |
| 21 | 9.6 | 8.473 | 0.883 | 2.002 | 0.585 | 12.571 |
| 19 | 8.39 | 8.473 | 1.010 | 2.290 | 0.669 | 14.384 |
| 14 | 5.66 | 8.473 | 1.497 | 3.395 | 0.992 | 21.322 |

<br /><br />

**Linear Actuator Stand Subsystem**
<br />
| Item | Testing Criteria | Testing Method | Measure of Success (MOS) | MOS Met? | What is needed for Improvement? |
|---|---|---|---|---|---|
| Linear Actuator Stand | The linear actuator is secured in a manner that the actuator and stand are anchored | Completion of repeated changes of linear actuator during operation | Actuator and stand does not move when during during operation of linear motor | Yes | Replace the stand top with 1 complete sheet of acrylic to strengthen |
| Linear Actuator Stand | The case of the linear actuator is grounded | Measure electrical continuity between actuator case and ground | Presense of electrical continuity from actuator to bike stand frame | Yes | No Improvements Necessary |
| Linear Actuator Stand | The linear actuator stand is to be sized for the motor controller to be stored inside of the stand | Visual inspection of stand and actuator controller | Actuator controller fits securely within the actuator stand | Yes | Replacing hook and loop attachment with 3.5 mm bolt and spacer to secure to the stand |
| Linear Actuator Stand | The linear actuator stand has two openings for the power and control wires | Visual Inspection of stand and wiring | Cables from actuator to controller and 12 VDC power supply cord are routed through holes within the stand  | Yes | |
| Linear Actuator Stand | The stand does not shield wireless communications of the motor controller | Manually send data to actuator controller wirelessly | Actuator recieves input from main raspberry pi with no greater than 40 ms latency | No | Troubleshoot and repair bluetooth code within the main raspberry pi. Motor controller does receive wireless communication from other devices such as phone via bluetooth |

<br /><br />

<br />
<br />

**Power Distribution Subsystem**
<br />
| Item | Testing Criteria | Testing Method | Measure of Success (MOS) | MOS Met? | What is needed for Improvement? |
|---|---|---|---|---|---|
| Circuit Design | Each power supply is to be adequately sized to be capable of carrying the maximum power requirement for all the devices within its respective circuit. | Review device datasheets and system wiring schematic | All devices are able to supply power at max load per device datasheets | Yes | Replace we a power supply that has multple output voltages to increase space in enclosure |
| Circuit Design | All wire sizing is to be in accordance with National Electrical Code Article 210.19(A)(1) based on continuous circuit load [1]. | Visually inspect all wiring powered by the power distribution system | All wiring has the capacity to carry 125% of maximum continous circuit load per device datasheets | Yes | No Improvements Required |
| Circuit Design | The system will maintain overprotection of the Mario Kart simulator devices with a rating of no less than %125 percent of maximum continuous circuit load as specified by the National Electrical Code Article 210.20(A) [1]. | Review device datasheets and system wiring schematic | Main circuit breaker overprotection is rated for at least 125% of maximum continous load | Yes | No Improvements Required |
| Safety | All 120 Vac terminals within the user interface are to have been covered and contain a warning of electrocution on the cover. | Visually inspect to ensure that front cover contains a warning label | Front panel has warning stating that cover to remain on at any time power cord is connected | Yes | Replace with a high gloss label |
| Safety | Power subsystem must include a means of de-energizing the system via circuit breaker lockout. | Visually inspect to ensure that the power has a means to be de-energized and locked out if needed | Power subsystem can be de-energized and locked out via electrical plug lockout | Yes | No Improvements Required |
| Safety | Circuit to include GFCI to ensure that all devices within the Mario Kart simulation are properly protected from ground faults. | Test GFCI to ensure that the system contains an operating GFCI | Presense of electrical continuity from the enclosure grounding bar to the ground pin of GFCI on power cord | Yes | No Improvements Required |
| Enclosure | The enclosure is to be sized to house all devices within the subsystem, excluding incoming and outgoing power cabling. | Visually inspect to ensure that the enclosure can contain all devices required for system operation | All devices within the enclosure fit without interference when front panel is closed | Yes | Installation of wire covers for appearances (cable trough) |
| Enclosure | The front panel containing the HMI is to be removable for access. | Visually inspect to ensure that the front panel contains the LCD in a secure manner and the panel can be removed | Front panel is removable by user or technician | Yes | Installation of gasket behind the LCD screen |
| Enclosure | The enclosure is to be fully enclosed and free of any openings. | Visually inspect to verify that the enclosure does not have any openings are gaps (excluding input and output wiring) | No gaps are present in enclosure and each hole in enclosure has a dedicated input or output wire(s) | Yes | Installation of 1 1/8" rubber grommet on 1 hole needed |
| Enclosure | The enclosure is to be properly grounded for protection to protect equipment and possible electrical shock. | Verify that the enclosure is properly ground to earth ground through the power cord by completing a continuity test between the linear actuator and the grounding location | Presence of electrical continuity from all grounding wires to grounding bar within enclosure | Yes | No Improvements Required |

<br /><br />

**HDMI Switcher Subsystem**
<br />
| Item | Testing Criteria | Testing Method | Measure of Success (MOS) | MOS Met? | What is needed for Improvement? |
|---|---|---|---|---|---|
| HDMI Compatibility | The BHS must be rated for 1080p resolutions. | Can assert this is met without testing (requires rating, is rated) | Has 1080p capacity | Yes | None |
| HDMI Quantity | The switcher must have at minimum two input HDMI ports and one output HDMI port. | Can assert this is met without testing (self-evident) | Possesses two HDMI inputs and one HDMI output | Yes | None |
| Relay Voltage/Current Ratings | The relay coil must be rated for 3.3 V and a maximum 16 mA, and the relay must operate at 3.3 V or below. | No longer valid as specification | No longer valid as specification | No | None |
| Transistor current | The transistor may not draw more than 16 mA, and the transistor must operate with a logic signal of 3.3 V | Review of datasheet | Can assert first by Ohm's Law; second is proven by minimal functionality | No | None |
| Relay Power Rating | The power dissipation at the relay coil cannot exceed 70 mW. | No longer valid as specification | No longer valid as specification | No | None |
| Back EMF Accommodations | A diode must be implemented in parallel with the relay coil to protect the RPi from back EMF that results from de-energizing the coil  | No longer valid as specification | No longer valid as specification | No | None |

<br /><br />

**Steering L Bracket Subsystem**
<br />
| System | Item | Testing Criteria | Testing Method | Measure of Success (MOS) | MOS Met? | What is needed for Improvement? |
|---|---|---|---|---|---|---|
| Steering L-Bracket Subsystem | Increased Fidelity | The Steering L-Bracket mechanism shall be strengthened using a metal component. | Visually inspect the steering sensor L-Bracket to ensure that it is composed of metal and secure | The L-Bracket is made of aluminum. The L-Bracket does not move when pressure is apllied to it. | Yes | No Improvement Required |
| Steering L-Bracket Subsystem | Adaptability to Steering Column | The L-Bracket must be positioned more than 0.25 inches off the steering column  | Measure the distance of the steering L-Bracket to the steering column and verify that the distance is more than 0.25 inches | The distance from the steering column to the L-bracket is 0.75 inches. | Yes | No Improvement Required |

<br /><br />

**Wireless Sensors Subsystem**
<br />

| Item | Testing Criteria | Testing Method | Measure of Success (MOS) | MOS Met? | What is needed for Improvement? |
|---|---|---|---|---|---|
| Run Time | Two weeks runtime with 4 hours continuous use each day | Verify that battery run time is efficient for two weeks with 4 hours a day of continous use by sampling power consumed while the system is in use and is inactive | Calculations confirm that the battery pack provides sufficient power. The steering sensor subsystem uses 3902.44 mW for 2 weeks of runtime while in constant use for 4 hours a day. The speed sensor subsystem uses 15292.71 mW for 2 weeks of runtime while in constant use for 4 hours a day. Each four AA battery pack provides 21000 mW, which is sufficient to meet the power requiremnets for each subsystem.  | Yes | The Arduino Nano 33 BLE for the speed sensor subsystem broke during testing. Replace the broken Arduino Nano 33 BLE in the speed sensor subsystem with the new one to make the subsystem bluetooth. |
| Speed Sensor (Missing MOSFET-Specific Requirements) | Obstacle sensor module provided with 20 mA @ 3.3 V - 5 V during operation | Complete game test: Measure the current at the Obstacle sensor to verfiy that the Obstacle sensor receives 20 mA @ 3.3 V- 5 V during operation | While the obstacle sensor is in operation, the current is 24 mA when the obstacle sensor is given 3.391 V. | Yes | Replace the tape on the tire with paint or design a new way to measure the speed. |
| Speed Sensor (Missing MOSFET-Specific Requirements) | Arduino Nano 33 BLE provided with DC voltage between 5 V and 21 V | Complete game test: Measure voltage at the Arduino Nano 33 BLE to verify that the Arduino Nano 33 BLE receives a voltage between 5 VDC and 21 VDC | With new batteries, the battery pack supplies more than 7 V to the Arduino Nano 33 BLE. | Yes | |
| Speed Sensor (Missing MOSFET-Specific Requirements) | Current through the 3.3 V output pin on the Arduino Nano 33 BLE must be less than 100 mA | Complete game test: Measure and verify that the current through the 3.3 V GPIO pin is less than 100 mA while in use | The current on the 3.3 V GPIO pin is 24 mA which is less than 100 mA. | Yes | |
| Steering Sensor | Potentiometer voltage same as ADC | Measure and verify that the voltage at the potentiometer is equal to the voltage at the ADC | The voltage on the potentiometer is 3.285 V which is the same as the voltage ADC which is 3.285 V. | Yes | Design a means to prevent the handlebar from turning 360 degrees. The potentiometer is not designed to turn 360 degrees. After the handle bar is turned past the potentiometer's limit, the potentiometer will break. Select a more durable potentiometer. The potentiometer on the bike broke during testing, and the spare broke during our presentation.  |
| Steering Sensor | ADC must be provided with a DC voltage between 0 - 5.5 V | Measure and verify that the voltage as seen by the ADC is within 0 VDC and 5.5 VDC | The voltage at the ADC is 3.285 V which is in between 0 VDC and 5.5 VDC. | Yes | |
| Steering Sensor | Current through every individual GPIO pin below 15 mA | Complete game test: Measure and verify that the current through each GPIO pin used in the system is below 15 mA | The current going through the GPIO pin is 4 mA which is less than 15 mA. | Yes | |
| Data Transfer | Wireless communication between sensors and main RPi for all sensors | Complete game test: Verify that there is communication between the main controller (RPI) and both speed sensor and steering sensor | Multiple races were played with wireless communication between the steering sensor (speed sensor radio chip was damaged before testing) | No | Wireless communication of the speed sensor still needs to be implemented. |
| Data Transfer | Maximum latency: 40 ms | Complete game test: Verify that the latency is less than 40 ms while the system is in normal operation | Using a stopwatch, the average latency was found to be much greater than 40 ms | No | The latency needs to be lowered significantly, perhaps with faster/more powerful hardware (RPi/Nano) or stronger Bluetooth signal. |
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

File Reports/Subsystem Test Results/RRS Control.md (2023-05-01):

# RRS Control Tests

**PWM Duty Cycle:**

In two trials testing both forward and reverse motion at the maximum output level, the PWM duty cycle of the voltage across the linear actuator was seen to be approximately 25 %. The oscilloscope captures below show the observed waveforms.

DS1Z_QuickPrint4

DS1Z_QuickPrint5

DS1Z_QuickPrint3

DS1Z_QuickPrint2

**Voltage ripple:**

Some voltage ripple may be seen on the output. Further testing on the power supply input to the controller, performed twice, reveals that the peak amplitude of the ripple is 8 V pk-pk.
For more detail, see the following oscilloscope captures:

DS1Z_QuickPrint2

DS1Z_QuickPrint1

DS1Z_QuickPrint6

**Stability:**

The device was tested across a range of different movement increments, and no instability was observed. See test demonstration video for details.
Test description: test for maximum extension, maximum retraction, middle point, movement by increments of 200 points, 100 points, 50 points, 25 points, 15 points. Ensure absence of undamped oscillation.

**Back-EMF Protection:**

The body diode foreward voltage was measured with an oscilloscope for each MOSFET in the design during operation for both extension and retraction, and the foreward voltage was always measured to be well below 1 V. See video for further detail.

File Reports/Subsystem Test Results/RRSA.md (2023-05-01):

# RRSA Testing

**Sync Test:**

For the initial test, recording was started, and the device was raised into the air 23 s after beginning recording. The collected video verifies that this is the timestamp at which the device was raised, and the collected data show a decrease in barometric pressure beginning at this time. The last data index corresponds to the ending timestamp of the video for both pressure and speed data.



Psync

A following test was used to further test syncing of the video footage to an external clock: start clock simultaneously to video recording, record clock.



This test produced the expected result.

In testing of the pressure sensor, similar correspondance of the change in elevation seen in the video and the change in pressure values was observed indicating successful syncing.
The sync was proven to be inadequite; however via 3 hour testing. In a 3 hour trial, the end result showed a final timestamp of 3:02:48 while the final data index was 110778 ds, indicating a desync of 110 s (where the data length is longer than the video). Reviewing the footage reveals that the video footage occasionally skips during recording, resulting in a shorter video relative to the collected data.

**Battery and Storage Test:**

The device was tested continuously recording for 3 hours. The device met specification in two trials, the results of which are below.

Trial 1:

    Vfinal (pi on) = 3.797 V
    On-board Charge Indication: 3/5
    Storage used: 8770091459 bytes (8.2 GiB)

Trial 2:

    Vfinal (pi on) = 3.729 V
		On-board Charge Indication: 3/5
		Storage used: 8913880643 bytes (8.3 GiB)

Based on the above storage usage, combined with the current storage usage, the device can store 42 hours worth of ride recordings.

Storage usage:

    Boot partition: 255 MiB
	  System files: 3586464503 bytes
	  Free Space (with no recordings): 115.5 GiB

**Durability Test:**

The device was sprayed down with water in a sink. The first trial was 5 min, the second 10 min. All functions were tested by recording during and after this, and no loss of functionality or damage was noted. To test the durability of the mounting bracket, the bike was ridden over gravel three times, then off the edge of the sidewalk. Following riding off the edge of the sidewalk, the mounting bracket broke, resulting in a failed test and preventing further durability testing.

**Altitude Sensing Precision Test:**

The device was raised 30 mm in three trials with the temperature controlled at 60 degrees F.

Trial 1:



    Start value: 975.489 hPa
    End value: 975.439 hPa
    Measured change in pressure: 0.050 hPa
    Ideal change in pressure: 0.034 hPa
    Corresponding change in altitude: 44.16 cm
    Error: 14.16 cm (rated error: 4.76 cm)

Trial 2:



    Start value: 974.970 hPa
    End value: 974.930 hPa
    Measured change in pressure: 0.040 hPa
    Ideal change in pressure: 0.034 hPa
    Corresponding change in altitude: 35.37 cm
    Error: 5.37 cm (rated error: 4.76 cm)

Trial 3:



    Start value: 975.237 hPa
    End value: 975.205 hPa
    Measured change in pressure: 0.032 hPa
    Ideal change in pressure: 0.034 hPa
    Corresponding change in altitude: 28.25 cm
    Error: 1.75 cm (rated error: 4.76 cm)

*Approximating elevation to be 970 hPa (literature value for Cookeville), T = 70 F, P0 = 1013.25 hPa*

In the first and second trials, significant error is observed relative to the specification. Analysis of the plots gives the impression that the measured pressure tends to drift with time, as the measured pressure changes significantly even at times when the device was not in motion.

**Pressure Accuracy Test:**

The accuracy of the pressure sensor was consistantly within 5 % of the literature value for Cookeville (all trials shown above count for this test, including the entirety of both 3 hour trials).

    Atmospheric pressure in Cookeville, TN: 97 kPa = 970 hPa [Source: https://elevation.maplogs.com/poi/cookeville_tn_usa.34896.html]
    Upper limit: 1018.5
    Lower limit: 921.5

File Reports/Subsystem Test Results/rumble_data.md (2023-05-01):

This document is meant to help quickly gain an understanding of how Joycontrol reports input and output data. In addition, this document will include where this data is located and how to utilize it.

**Getting Started**

Firstly, when connecting the bike to the switch using the sudo python3 run_controller_cli.py command, it is necessary to include the -l flag followed by a file name for the information to go to. This looks like the following:

sudo python3 run_controller_cli.py PRO_CONTROLLER -l myreport

It is also better to not use .txt files or anything similar. Stick with either .hex, .bin, or extensionless files.

To view the hex code that is exported, a dedicated hex editor is necessary. Installed onto the Raspberry Pi OS that is with the MK/RRS bike is the Bless hex editor, although any hex editor will do. Bless can be opened by simply typing "bless" into the terminal. When working on Windows devices, Notepad++ with the Hex Editor plugin works well. This can be obtained through the plugin tab via plugin à plugin admin.

**Report Basics**

The communications between the Nintendo Switch and the controller can be seen via the report, as referenced above. The report presents an input and an output report, distinguished by a leading byte 0xA1 and 0xA2, respectively. For rumble data purposes, the output report is the only one to be considered. For output reports, there are several different output reports, all of which can be found at <https://github.com/dekuNukem/Nintendo_Switch_Reverse_Engineering/blob/master/bluetooth_hid_notes.md>. However, the two most common output reports are subcommand reports and rumble data reports, marked by a second byte of 0x01 and 0x10, respectively.

**Rumble Data Formatting**

            The output reports for rumble data are 23-byte values. The values of interest, however, can be obtained from the first eleven bytes. A simple description of the format will be performed using an example value in hexadecimal:

A2       10        03        62        18        63        40        62        18        63        40

Where:

- A2: Report type. This describes whether it is an output or input report. In this case, it is an output report.

- 10: Output type. This shows what kind of output data is being shown. This is rumble data in this case.

- 03: Counter. This value increments from 0x00 to 0x0F, resetting once it surpasses 0x0F. This is seemingly to ensure the proper rumble data output occurs in sequence.

- 62 18 63 40: Rumble data. This is the primary value that describes the rumble data characteristics. The first four values is for the left joycon, and the second four is for the right joycon. In the case of a pro controller, this is for the left and right rumble packs, respectively. In all cases, the first four bytes repeat for the second four.

For a more thorough description of rumble data in an output report, visit <https://github.com/dekuNukem/Nintendo_Switch_Reverse_Engineering/blob/master/bluetooth_hid_notes.md>. For a description of rumble data in general, visit <https://github.com/dekuNukem/Nintendo_Switch_Reverse_Engineering/blob/master/rumble_data_table.md>. For the purposes of Revision 2 of this project, the in-depth information found in those web pages are not necessary.

**What's Going On?**

            The first thing to note is that there is a persistent rumble data value of 00 01 40 40. This is effectively the rumble's resting state. This value means no rumble is present. This is useful as it presents a method of informing the resistance system when it does not need to be in use. Conversely, any instance that does not present this value needs to be addressed.

            Next, it is important to note that the rumble data does not present a constant value or a constant order. Rather, it sends a group of rumble patterns in a randomized order. These values are recognizable and can be used to determine what in-game instance is occurring. For the purposes of the prototype, there is a focus on the off-road rumble data. Some distinct rumble patterns from Moo Moo Meadows are as follows:

67        37        B7       58

00        01        40        40

CA       8D       61        40

DC       00        3D       40

00        01        40        40

62        18        63        40

B0       00        38        40

This is beneficial because, in the case of driving off-road, a distinct pattern or value can be found, then the resistance can be applied until the user is back on the track. Since the resting value is part of the rumble patterns for being off-road, it can be determined that the user is on the track again after two or more instances of 00 01 40 40 are detected.

            An issue that needs to be addressed is that different stages have variations in rumble data. For example, Dry Dry Desert has the following off-road rumble data:

CA       8A       49        40

CA       8A       61        40

DC       00        BD       4B

DC       00        BD       49

67        29        AF       58

It can also be seen that some rumble states are identical to those found in Moo Moo Meadows. There are also several repeated first bytes, such as 62, 63, 6F, CA, DC, 80, and 67.

            Finally, testing was performed in the Mario Circuit track, the results being many of the same rumble states as are found in Moo Moo Meadows. There are some unique states, but the CA 8D 61 40, DC 00 3D 40, 00 01 40 40 pattern and the 67 37 B7 58, 00 01 40 40 pattern both appear. This indicates that grass, sand, and other types of offroad terrain have their own rumble state lists that, though very similar, are not the same. However, both sand and grass offroad terrains have a commonality in that the fourth bytes of 40, 80, and 58 occur very frequently. Offroad instances can therefore be determined primarily by finding the first byte pattern CA followed by DC, the first byte 67 paired with the fourth byte 58, or an instance of a triad of a combination of 40, 80, or 58. Other values occur, but they occur too rarely to cause concern.

            For being hit by a shell, a unique rumble state of

80        6A       60        80

appeared at or near the beginning of the set of rumble data sent for all three recorded instances of being hit by a shell. This implies that shell collisions always results in this rumble data string being sent to the output report. Additionally, being hit by a shell, when compared to offroad and boost instances, presents the widest variation of fourth byte values. Particularly, the last four bits are the most random out of the three rumble state instances considered here. Finally, the null state does not occur at any point in the patterns. It appears that a shell collision can be detected via the rumble state above. As a fallback, three rumble states where the last four bits do not repeat without either the null state or a fourth byte of 40, 80, 71, or 72 occurring. The purpose of including 71 and 72 can be found below.

            For boosting with a mushroom, the rumble states are the most inconsistent. Between two sets of boost data, only one value was repeated, that value being

78        00        2X       72

where the X represents the numbers 6, 8, or 9, as those are the only ones that occurred. This value was also only found in the first boost's set of rumble data, meaning that it is unreliable and, therefore, unusable. However, there are attributes that makes these states easy to identify. The first byte has the most values between 90 and 9F. More interestingly, the fourth byte only exceeded 7F twice across two boost values, with values 71 and 72 occurring frequently.

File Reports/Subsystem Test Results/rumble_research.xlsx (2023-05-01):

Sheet: moomooben1
Bytes
0 | 1 | 2 | 3 | 4 | 5 | 6 | 7 | 8 | 9 | 10 | 11 | 12 | 13
A2 | 01 | 0E | 00 | 00 | 00 | 00 | 00 | 00 | 00 | 00 | 02 | 00 | 00
A2 | 01 | 0F | 00 | 00 | 00 | 00 | 00 | 00 | 00 | 00 | 08 | 00 | 00
A2 | 01 | 00 | 00 | 00 | 00 | 00 | 00 | 00 | 00 | 00 | 10 | 00 | 60
A2 | 01 | 01 | 00 | 00 | 00 | 00 | 00 | 00 | 00 | 00 | 10 | 50 | 60
A2 | 01 | 02 | 00 | 01 | 40 | 40 | 00 | 01 | 40 | 40 | 03 | 30 | 00
A2 | 01 | 03 | 00 | 00 | 00 | 00 | 00 | 00 | 00 | 00 | 04 | 00 | 00
A2 | 01 | 04 | 00 | 00 | 00 | 00 | 00 | 00 | 00 | 00 | 10 | 80 | 60
A2 | 01 | 05 | 00 | 00 | 00 | 00 | 00 | 00 | 00 | 00 | 10 | 98 | 60
A2 | 01 | 06 | 00 | 00 | 00 | 00 | 00 | 00 | 00 | 00 | 10 | 10 | 80
A2 | 01 | 07 | 00 | 00 | 00 | 00 | 00 | 00 | 00 | 00 | 10 | 3D | 60
A2 | 01 | 08 | 00 | 00 | 00 | 00 | 00 | 00 | 00 | 00 | 10 | 20 | 60
A2 | 10 | 09 | 00 | 01 | 40 | 40 | 00 | 01 | 40 | 40 | 6D | D4 | 6C
A2 | 01 | 0A | 00 | 00 | 00 | 00 | 00 | 00 | 00 | 00 | 40 | 02 | 00
A2 | 01 | 0B | 00 | 00 | 00 | 00 | 00 | 00 | 00 | 00 | 48 | 01 | 00
A2 | 01 | 0C | C2 | 18 | 03 | 72 | 00 | 01 | 40 | 40 | 21 | 21 | 00
A2 | 01 | 0D | 00 | 01 | 40 | 40 | 00 | 00 | 00 | 00 | 30 | 01 | 00
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

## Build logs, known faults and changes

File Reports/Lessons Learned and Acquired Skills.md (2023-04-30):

# Lessons Learned and Acquired Skills

## Tyler Chittum
### Lessons
1. Limitations of mechanical durability: the mounting bracket for the RRSA subsystem unexpectedly broke rather easily during testing by riding off a curb. This occured because the mounting bracket was too weak, the mounting location was not at the center of gravity, and the bike used lacked any form of damping on the suspension. In addition, the glue used to attempt to repair it did not hold, and in fact failed to harden normally. The five-minute epoxy we used seems to have been a bad batch. A sturdier mounting bracket or more centered mounting location may have averted this issue.
2. Limitations of Raspberry Pi video recording: the Raspberry Pi used in the RRSA subsystem unexpectedly drops frames during recordings. This results in desync with the data which cannot be resolved by simply shifting or clipping the data.
3. Pressure sensing requires airflow to the sensor.
4. It is important to use ESD protection to avoid damaging components. A failure to adequitely protect against ESD unexpectedly resulted in the failure of two key components (ADC and Arduino Nano).
6. Limitations of Raspberry Pi video playback: the Raspberry Pi has some rather shoddy video playback, and the one in use as the main controller in this project is all the less capable given that it is running a desktop operating system.
7. Always get permission before touching other people's work.
8. The manufacturer-provided PID coefficients for the utilized actuator did not provide stable operation using our controller, which meant that we had to manually tune the device.
9. As per Mr. Roberts advice: linear actuator duty cycle is not a valid rating on a very minute timescale, which is to say that PWM duty cycle is not a valid means to meet such a specification as was done for the RRS control subsystem.
10. In terms of management, we found having no leader to work fine, but I feel that teamwork was much more effective when decisions regarding who would do what were made at meetings rather than left up to whoever decided to take action.
11. Communication was most effective when going through only one channel.
12. If you feel stuck, it is a good idea to ask others for help, and you should always be willing to help as well.
13. The pin socket header used to connect the wireless module on the RRS controller subsystem is too short, and does not do a good job of holding the wireless module or normal wire pins, particularly when the enclosure vibrates. The lesson here is that deeper pin sockets are better.
### Acquired Skills
1. 3D modeling for signoffs.
2. Teamwork, particularly getting a feel for when it is or isn't beneficial to try to help.
3. Presenting, which was required several times throughout the process.
4. Time management; particularly knowing when to give up/ignore things when not doing so would result in worse overall consequences due to eating into time needed for more important tasks.

## Ray Durlin
### Lessons learned
1. It is important to be as detailed as possible in the design phase of a project to ensure that the implementation is better efficient
2. Project outcome identification and analyzing measure of success
3. Better understanding of how to meet deadlines and expectations 
4. Importance of teamwork in a group setting
5. Presenting work to different types of audiences
6. Effectively communicating with others
7. How to be a better problem solver
8. Value of overcoming obstacles
9. Do not be afraid to ask for help
10. Allows look for better ways to improve, countinous improvement will lead to a desireable outcome
11. When in doubt, look at the manufacturers datasheet, or call the manufacture to ask questions - Use all the resources available

### Skills Acquired
1. AutoCAD 
2. Project Design
3. Detailed knowledge of GFCI and Overprotection
4. Fabricating components
5. Hands on system implementation
6. Analysis and Experimentation
7. Theoretical Modeling
8. MATLAB – Simulink
9. Electrical troubleshooting

## Blake Pickett
### Lessons
1. Impact of Logistics on project success
2. Effective collaboration and communication are critical
3. Clear, concise, and up-to-date documentation is critical
4. Better understanding of Eddy Currents and Magnetic Fields
5. Better understanding of Bluetooth Communication and how Arduinos work
6. Better understanding of how a Potentiometer works
7. Better understanding of Battery Power Supply
8. Better understanding of the impacts of Procurement process
9. Backup plan is necessary for Risk Mitigation (e.g., technical performance, parts/supplies delivery, etc.)

### Skills Acquired
1. Power estimation and supply for Electronics
2. Arduino installation
3. AutoCAD
4. Design implementation and fabrication (e.g., L-Bracket, Flywheel, Magnet Bracket, Actuator Bracket)
5. Testing, analysis and experimentation
6. Troubleshooting
7. Improved Soldering skills for Electronics application
8. Improved Technical Writing skills (e.g., proposal, reports)
9. Electronic subsystem removal and documentation 
10. Integration of new Subsystem components with existing components 

## Sage Mooneyham
### Lessons
1.	Some hardware can be unexpectedly fragile
2.	Software libraries are very helpful
3.	RPi’s are quite finnicky
4.	It’s important to constantly have backups (plans, files, etc.)
5.	When picking up another teams work, it’s beneficial to have contact with the previous team
6.	Reading data sheets is important

### Skills Acquired
1.	Bluetooth programming
2.	Python programming
3.	Design Implementation
4.	Debugging
5.	Command terminal navigation
6.	Arduino Nano programming
7.	Incorporating someone else’s work in your own
8.	Serial communication
9.	Time management
10.	Presenting
11.	Working in a team

## Benjamin Reed
### Lessons
1. When inheriting a project from another team, it is imperative that determination of how the hardware and software works occur very early in the development process. 
2. Adequate documentation is necessary to allow future teams to be able to improve the design properly. 
3. If utilizing any video, ensure that the hardware you are using, specifically the graphics card, is capable of handling the video you intend to use. 
4. Software development needs to begin very early. Even as early as the conceptual design. 
5. Go ahead and have a basic idea of how you could run experiments on hardware during the design phase to have a head start. 
6. If a software component is imperative for the function of your design, then checking if that component can be used should be considered part of that design. 
7. It is important to understand the schedules of your teammates and to plan the project accordingly to those schedules. 
8. In addition to the importance of documentation, it is as important to document while designing, researching, and building for the project. 
9. If you have a plan, there is a very good chance that plan does not come to fruition. It is, however, better than having no plan and, therefore, no direction. 
10. I cannot stress enough the importance of documentation. Nobody is going to think the way you do, so every detail needs to be discussed and conveyed in a digestible manner. 
11. It is important to state everything explicitly. Even if information can be assumed, such as hardware having the appropriate specifications according to their datasheets, the fact that it has room to be assumed introduces an unnecessary possibility of error. 

### Skills Acquired
1. Reverse-engineering the work of a previous design. 
2. Hardware design and datasheet analysis. 
3. Python GUI development via the TKinter package. 
4. Python video manipulation via the VLC package. 
5. Skills associated with presenting to an audience. 
6. Skills associated with working with a team. 
7. Programming for a Raspberry Pi. 
8. Hardware testing and analysis. 
9. Conveying complex ideas to individuals that lack the knowledge you possess.

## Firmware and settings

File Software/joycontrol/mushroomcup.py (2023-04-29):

# Imports
import serial
import time

# Constants for Linear Actuator positions
NOMINAL = b'1'
NO_RES = b'300'
SMALL_HILL = b'600'
MED_HILL = b'650'
BIG_HILL = b'675'
WATER = b'675'
WATER_HILL = b'725'
SODA = b'750'

motorCon = serial.Serial('/dev/ttyS0', 9600, timeout=0.01)
motorCon.reset_input_buffer()

def mk_stadium():
    enterCheck = input("Press Enter when race is starting.")
    if enterCheck == "":
        print("Race at Mario Kart Stadium is starting...")
        time.sleep(4)
        motorCon.write(NO_RES)
        print('3!')
        time.sleep(1)
        print('2!')
        time.sleep(1)
        print('1!')
        time.sleep(1)
        print("GO!")
        for i in range(0, 3):
            motorCon.write(NO_RES)
            time.sleep(13)
            motorCon.write(SMALL_HILL)
            time.sleep(9)
            motorCon.write(NO_RES)
            time.sleep(5)
            motorCon.write(BIG_HILL)
            time.sleep(6)
            motorCon.write(NO_RES)
            time.sleep(9)
            motorCon.write(SMALL_HILL)
            time.sleep(2)
            motorCon.write(NO_RES)
            time.sleep(2)
    motorCon.write(NOMINAL)
    print("Race complete!")
    time.sleep(3)

    enterCheck = input("Press Enter when race is starting.")
    if enterCheck == "":
        return

def water_park():
    print("Race at Water Park is starting...")
    time.sleep(4)
    motorCon.write(NO_RES)
    print('3!')
    time.sleep(1)
    print('2!')
    time.sleep(1)
    print('1!')
    time.sleep(1)
    print("GO!")
    for i in range(0, 3):
        motorCon.write(NO_RES)
        time.sleep(3)
        motorCon.write(SMALL_HILL)
        time.sleep(1)
        motorCon.write(NO_RES)
        time.sleep(6)
        motorCon.write(MED_HILL)
        time.sleep(4)
        motorCon.write(WATER)
        time.sleep(4)
        motorCon.write(WATER_HILL)
        time.sleep(2)
        motorCon.write(BIG_HILL)
        time.sleep(7)
        motorCon.write(NO_RES)
        time.sleep(4)
        motorCon.write(WATER)
        time.sleep(9)
        motorCon.write(WATER_HILL)
        time.sleep(2)
        motorCon.write(NO_RES)
        time.sleep(6)
    motorCon.write(NOMINAL)
    print("Race complete!")
    time.sleep(3)
    enterCheck = input("Press Enter when race is starting.")
    if enterCheck == "":
        return
    
def ss_canyon():
    print("Race at Sweet Sweet Canyon is starting...")
    time.sleep(4)
    motorCon.write(NO_RES)
    print('3!')
    time.sleep(1)
    print('2!')
    time.sleep(1)
    print('1!')
    time.sleep(1)
    print("GO!")
    for i in range(0, 3):
        motorCon.write(SMALL_HILL)
        time.sleep(11)
        motorCon.write(NO_RES)
        time.sleep(10)
        motorCon.write(SODA)
        time.sleep(6)
        motorCon.write(BIG_HILL)
        time.sleep(5)
        motorCon.write(NO_RES)
        time.sleep(7)
        motorCon.write(MED_HILL)
        time.sleep(2)
        motorCon.write(SMALL_HILL)
        time.sleep(2)
        motorCon.write(MED_HILL)
        time.sleep(1)
        motorCon.write(NO_RES)
        time.sleep(4)
    motorCon.write(NOMINAL)
    print("Race complete!")
    time.sleep(3)
    enterCheck = input("Press Enter when race is starting.")
    if enterCheck == "":
        return
    
def thwomp_ruins():
    print("Race at Thwomp Ruins is starting...")
    time.sleep(4)
    motorCon.write(NO_RES)
    print('3!')
    time.sleep(1)
    print('2!')
    time.sleep(1)
    print('1!')
    time.sleep(1)
    print("GO!")
    for i in range(0, 3):
        motorCon.write(NO_RES)
        time.sleep(3)
        motorCon.write(SMALL_HILL)
        time.sleep(8)
        motorCon.write(NO_RES)
        time.sleep(11)
        motorCon.write(MED_HILL)
        time.sleep(2)
        motorCon.write(NO_RES)
        time.sleep(5)
        motorCon.write(SMALL_HILL)
        time.sleep(8)
        motorCon.write(BIG_HILL)
        time.sleep(5)
        motorCon.write(NO_RES)
        time.sleep(9)
    motorCon.write(NOMINAL)
    print("Race complete!")
    time.sleep(10)

def main():
    print("Thank you for using the Mario Kart Exercise Bike!")
    mk_stadium()
    water_park()
    ss_canyon()
    thwomp_ruins()
    print("Mushroom Cup Complete!")

if __name__ == "__main__":
    main()

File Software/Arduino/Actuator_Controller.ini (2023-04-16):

#include <PID_v1.h>

int forward_en = 3;//Drives Q1
int reverse_en = 2;//Drives Q2
int forward_PWM = 6;//Drives Q4
int reverse_PWM = 5;//Drives Q3
int potentiometer = A4;
double setpoint = 22, feedback, output; //PID parameters
double setpoint_new; //To allow conditional acceptance of setpoint
PID act_PID(&feedback, &output, &setpoint, 0.96, 8.6, 0.036, DIRECT); //DIRECT is correlation of actuator movement to error (opposed to REVERSE)
bool forward_last; //Tracks the previous directional setting to allow switching delay

void setup() {
  digitalWrite(forward_en, LOW);
  digitalWrite(reverse_en, LOW);
  analogWrite(forward_PWM, 0);
  analogWrite(reverse_PWM, 0);
  pinMode(forward_en, OUTPUT);
  pinMode(reverse_en, OUTPUT);
  pinMode(forward_PWM, OUTPUT);
  pinMode(reverse_PWM, OUTPUT);
  Serial.begin(9600);
  Serial.setTimeout(100);
  act_PID.SetMode(AUTOMATIC);
  act_PID.SetOutputLimits(-63, 63);//Sets max duty cycle to 25 %
  act_PID.SetSampleTime(12);//The time between each PID evaluation in milliseconds

}

/*
 * Conditions which must be avoided: forward_en &&
 * reverse_PWM, reverse_en && forward_PWM.
 * The value of the feedback signal is to increase
 * as the actutator moves in the forward direction.
 */

void loop() {
  feedback = analogRead(potentiometer);//Feedback from ADC reading of actuator feedback signal
  setpoint_new = Serial.parseInt(); //Receive new setpoint over serial Bluetooth connection
  if(setpoint_new != 0){//Conditional - use to define allowable range for setpoint
  //if(setpoint_new > 554)
  //  setpoint = 554;
  //else
    setpoint = setpoint_new;
  }
  
//Serial.println(feedback); //FOR TESTING - TEMPORARY
  act_PID.Compute();

  //Executed for positive error; produces forward motion
  if(setpoint > feedback && forward_last){
    //These first two lines are only included as a safety measure 
    digitalWrite(reverse_en, LOW);
    analogWrite(reverse_PWM, 0);

    if(output < 10)//Prevents operation of actuator when output is too low to effect motion
      output = 0;
    analogWrite(forward_PWM, output);
    digitalWrite(forward_en, HIGH);
//  Serial.print(output);//FOR TESTING ONLY
    forward_last = 1;
  }

//Executed for negative error; produces reverse motion
  else if(setpoint < feedback && !forward_last){
    //These first two lines are only included as a safety measure
    digitalWrite(forward_en, LOW);
    analogWrite(forward_PWM, 0);

    if(output > -10)//Prevents operation of actuator when output is too low to effect motion
      output = 0;
    analogWrite(reverse_PWM, abs(output));
    digitalWrite(reverse_en, HIGH);
//  Serial.print(output);
    forward_last = 0;
  }
  
//Executed for zero error or when a delay is needed for switching directions; halts the actuator
  else{
    digitalWrite(forward_en, LOW);
    digitalWrite(reverse_en, LOW);
    analogWrite(forward_PWM, 0);
    analogWrite(reverse_PWM, 0);
    delayMicroseconds(100);//Switching delay; increase if transistors get warm during direction changes
    forward_last = !forward_last;
    
  }

}

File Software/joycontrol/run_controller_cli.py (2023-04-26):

#!/usr/bin/env python3

import argparse
import asyncio
import logging
import os

from aioconsole import ainput

import joycontrol.debug as debug
from joycontrol import logging_default as log, utils
from joycontrol.command_line_interface import ControllerCLI
from joycontrol.controller import Controller
from joycontrol.controller_state import ControllerState, button_push, button_press, button_release
from joycontrol.memory import FlashMemory
from joycontrol.protocol import controller_protocol_factory
from joycontrol.server import create_hid_server
from joycontrol.nfc_tag import NFCTag

logger = logging.getLogger(__name__)


"""Emulates Switch controller. Opens joycontrol.command_line_interface to send button commands and more.

While running the cli, call "help" for an explanation of available commands.

Usage:
    run_controller_cli.py <controller> [--device_id | -d  <bluetooth_adapter_id>]
                                       [--spi_flash <spi_flash_memory_file>]
                                       [--reconnect_bt_addr | -r <console_bluetooth_address>]
                                       [--log | -l <communication_log_file>]
                                       [--nfc <nfc_data_file>]
    run_controller_cli.py -h | --help

Arguments:
    controller      Choose which controller to emulate. Either "JOYCON_R", "JOYCON_L" or "PRO_CONTROLLER"

Options:
    -d --device_id <bluetooth_adapter_id>   ID of the bluetooth adapter. Integer matching the digit in the hci* notation
                                            (e.g. hci0, hci1, ...) or Bluetooth mac address of the adapter in string
                                            notation (e.g. "FF:FF:FF:FF:FF:FF").
                                            Note: Selection of adapters may not work if the bluez "input" plugin is
                                            enabled.

    --spi_flash <spi_flash_memory_file>     Memory dump of a real Switch controller. Required for joystick emulation.
                                            Allows displaying of JoyCon colors.
                                            Memory dumps can be created using the dump_spi_flash.py script.

    -r --reconnect_bt_addr <console_bluetooth_address>  Previously connected Switch console Bluetooth address in string
                                                        notation (e.g. "FF:FF:FF:FF:FF:FF") for reconnection.
                                                        Does not require the "Change Grip/Order" menu to be opened,

    -l --log <communication_log_file>       Write hid communication (input reports and output reports) to a file.

    --nfc <nfc_data_file>                   Sets the nfc data of the controller to a given nfc dump upon initial
                                            connection.
"""


async def test_controller_buttons(controller_state: ControllerState):
    """
    Example controller script.
    Navigates to the "Test Controller Buttons" menu and presses all buttons.
    """
    if controller_state.get_controller() != Controller.PRO_CONTROLLER:
        raise ValueError('This script only works with the Pro Controller!')

    # waits until controller is fully connected
    await controller_state.connect()

    await ainput(prompt='Make sure the Switch is in the Home menu and press <enter> to continue.')

    """
    # We assume we are in the "Change Grip/Order" menu of the switch
    await button_push(controller_state, 'home')

    # wait for the animation
    await asyncio.sleep(1)
    """

    # Goto settings
    await button_push(controller_state, 'down', sec=1)
    await button_push(controller_state, 'right', sec=2)
    await asyncio.sleep(0.3)
    await button_push(controller_state, 'left')
    await asyncio.sleep(0.3)
    await button_push(controller_state, 'a')
    await asyncio.sleep(0.3)

    # go all the way down
    await button_push(controller_state, 'down', sec=4)
    await asyncio.sleep(0.3)

    # goto "Controllers and Sensors" menu
    for _ in range(3):
        await button_push(controller_state, 'up')
        await asyncio.sleep(0.3)
    await button_push(controller_state, 'right')
    await asyncio.sleep(0.3)

    # go all the way down
    await button_push(controller_state, 'down', sec=3)
    await asyncio.sleep(0.3)

    # goto "Test Input Devices" menu
    await button_push(controller_state, 'up')
    await asyncio.sleep(0.3)
    await button_push(controller_state, 'a')
    await asyncio.sleep(0.3)

    # goto "Test Controller Buttons" menu
    await button_push(controller_state, 'a')
    await asyncio.sleep(0.3)

    # push all buttons except home and capture
    button_list = controller_state.button_state.get_available_buttons()
    if 'capture' in button_list:
        button_list.remove('capture')
    if 'home' in button_list:
        button_list.remove('home')

    user_input = asyncio.ensure_future(
        ainput(prompt='Pressing all buttons... Press <enter> to stop.')
    )

    # push all buttons consecutively until user input
    while not user_input.done():
        for button in button_list:
            await button_push(controller_state, button)
            await asyncio.sleep(0.1)

            if user_input.done():
                break

    # await future to trigger exceptions in case something went wrong
    await user_input

    # go back to home
    await button_push(controller_state, 'home')


def ensure_valid_button(controller_state, *buttons):
    """
    Raise ValueError if any of the given buttons os not part of the controller state.
    :param controller_state:
    :param buttons: Any number of buttons to check (see ButtonState.get_available_buttons)
    """
    for button in buttons:
        if button not in controller_state.button_state.get_available_buttons():
            raise ValueError(f'Button {button} does not exist on {controller_state.get_controller()}')


async def mash_button(controller_state, button, interval):
    # wait until controller is fully connected
    await controller_state.connect()
    ensure_valid_button(controller_state, button)

    user_input = asyncio.ensure_future(
        ainput(prompt=f'Pressing the {button} button every {interval} seconds... Press <enter> to stop.')
    )
    # push a button repeatedly until user input
    while not user_input.done():
        await button_push(controller_state, button)
        await asyncio.sleep(float(interval))

    # await future to trigger exceptions in case something went wrong
    await user_input
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

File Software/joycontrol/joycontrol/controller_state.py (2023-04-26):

import asyncio

from joycontrol import utils
from joycontrol.controller import Controller
from joycontrol.memory import FlashMemory


class ControllerState:
    def __init__(self, protocol, controller: Controller, spi_flash: FlashMemory = None):
        self._protocol = protocol
        self._controller = controller
        self._nfc_content = None

        self._spi_flash = spi_flash

        self.button_state = ButtonState(controller)

        # create left stick state
        self.l_stick_state = self.r_stick_state = None
        if controller in (Controller.PRO_CONTROLLER, Controller.JOYCON_L):
            # load calibration data from memory
            calibration = None
            if spi_flash is not None:
                calibration_data = spi_flash.get_user_l_stick_calibration()
                if calibration_data is None:
                    calibration_data = spi_flash.get_factory_l_stick_calibration()
                calibration = LeftStickCalibration.from_bytes(calibration_data)

            self.l_stick_state = StickState(calibration=calibration)
            if calibration is not None:
                self.l_stick_state.set_center()

        # create right stick state
        if controller in (Controller.PRO_CONTROLLER, Controller.JOYCON_R):
            # load calibration data from memory
            calibration = None
            if spi_flash is not None:
                calibration_data = spi_flash.get_user_r_stick_calibration()
                if calibration_data is None:
                    calibration_data = spi_flash.get_factory_r_stick_calibration()
                calibration = RightStickCalibration.from_bytes(calibration_data)

            self.r_stick_state = StickState(calibration=calibration)
            if calibration is not None:
                self.r_stick_state.set_center()

        self.sig_is_send = asyncio.Event()

    def get_controller(self):
        return self._controller

    def get_flash_memory(self):
        return self._spi_flash

    def set_nfc(self, nfc_content):
        self._nfc_content = nfc_content

    def get_nfc(self):
        return self._nfc_content

    async def send(self):
        """
        Invokes protocol.send_controller_state(). Returns after the controller state was send.
        Raises NotConnected exception if the connection was lost.
        """
        await self._protocol.send_controller_state()

    async def connect(self):
        """
        Waits until the switch is paired with the controller and accepts button commands
        """
        await self._protocol.sig_input_ready.wait()


class ButtonState:
    """
    Utility class to set buttons in the input report
    https://github.com/dekuNukem/Nintendo_Switch_Reverse_Engineering/blob/master/bluetooth_hid_notes.md
    Byte 	0 	    1 	    2 	    3 	    4 	    5 	    6 	    7
    1   	Y 	    X 	    B 	    A 	    SR 	    SL 	    R 	    ZR
    2       Minus 	Plus 	R Stick L Stick Home 	Capture
    3       Down 	Up 	    Right 	Left 	SR 	    SL 	    L 	    ZL

    Example for generated methods: home button (byte_2, 4)

    def home(self, pushed=True):
        if pushed != utils.get_bit(self.byte_2, 4):
            self.byte_2 = utils.flip_bit(self.byte_2, 4)

    def home_is_set(self):
        return get_bit(self.byte_2, 4)
    """
    def __init__(self, controller: Controller):
        self.controller = controller

        # 3 bytes
        self._byte_1 = 0
        self._byte_2 = 0
        self._byte_3 = 0

        # generating methods for each button
        def button_method_factory(byte, bit):
            def setter(pushed=True):
                _byte = getattr(self, byte)

                if pushed != utils.get_bit(_byte, bit):
                    setattr(self, byte, utils.flip_bit(_byte, bit))

            def getter():
                return utils.get_bit(getattr(self, byte), bit)
            return setter, getter

        if self.controller == Controller.PRO_CONTROLLER:
            self._available_buttons = {'y', 'x', 'b', 'a', 'r', 'zr',
                                       'minus', 'plus', 'r_stick', 'l_stick', 'home', 'capture',
                                       'down', 'up', 'right', 'left', 'l', 'zl'}
        elif self.controller == Controller.JOYCON_R:
            self._available_buttons = {'y', 'x', 'b', 'a', 'sr', 'sl', 'r', 'zr',
                                       'plus', 'r_stick', 'home'}
        elif self.controller == Controller.JOYCON_L:
            self._available_buttons = {'minus', 'l_stick', 'capture',
                                       'down', 'up', 'right', 'left', 'sr', 'sl', 'l', 'zl'}

        # byte 1
        if self.controller == Controller.PRO_CONTROLLER or self.controller == Controller.JOYCON_R:
            self.y, self.y_is_set = button_method_factory('_byte_1', 0)
            self.x, self.x_is_set = button_method_factory('_byte_1', 1) #1
            self.b, self.b_is_set = button_method_factory('_byte_1', 2)
            self.a, self.a_is_set = button_method_factory('_byte_1', 3) #3

            if self.controller == Controller.JOYCON_R:
                self.sr, self.sr_is_set = button_method_factory('_byte_1', 4)
                self.sl, self.sl_is_set = button_method_factory('_byte_1', 5)

            self.r, self.r_is_set = button_method_factory('_byte_1', 6)
            self.zr, self.zr_is_set = button_method_factory('_byte_1', 7)

        # byte 2
        self.minus, self.minus_is_set = button_method_factory('_byte_2', 0)
        self.plus, self.plus_is_set = button_method_factory('_byte_2', 1)
        self.r_stick, self.r_stick_is_set = button_method_factory('_byte_2', 2)
        self.l_stick, self.l_stick_is_set = button_method_factory('_byte_2', 3)
        if self.controller == Controller.JOYCON_R or self.controller == Controller.PRO_CONTROLLER:
            self.home, self.home_is_set = button_method_factory('_byte_2', 4)
        if self.controller == Controller.JOYCON_L or self.controller == Controller.PRO_CONTROLLER:
            self.capture, self.capture_is_set = button_method_factory('_byte_2', 5)

        # byte 3
        if self.controller == Controller.PRO_CONTROLLER or self.controller == Controller.JOYCON_L:
            self.down, self.down_is_set = button_method_factory('_byte_3', 0)
            self.up, self.up_is_set = button_method_factory('_byte_3', 1)
            self.right, self.right_is_set = button_method_factory('_byte_3', 2)
            self.left, self.left_is_set = button_method_factory('_byte_3', 3)

            if self.controller == Controller.JOYCON_L:
                self.sr, self.sr_is_set = button_method_factory('_byte_3', 4)
                self.sl, self.sl_is_set = button_method_factory('_byte_3', 5)

            self.l, self.l_is_set = button_method_factory('_byte_3', 6)
            self.zl, self.zl_is_set = button_method_factory('_byte_3', 7)
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

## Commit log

2022-11-22 Create Mario Kart Rev 2 - Signoff - Mario Kart Bike Wireless Sensors Subsystem.md
    Requesting signoff for Mario Kart Bike Wireless Sensors Subsystem
2022-11-22 benjaminreed-signoff-hdmiswitcher
    Requesting Signoff for HDMI Switcher
2022-11-22 PowerDistributionSystem-signoff-subsystem
    Requesting sign off for the power distribution subsystem
2022-12-01 Create Resistance
2022-12-07 Change to minimum tire speed section
    Removed the section which said the resistance would drop off to the lowest possible value immediately after the bike wheel goes slower than what corresponds to 9 mi/h
2022-12-07 Requesting Signoff for Ride Resistance System Control Circuit
2023-01-13 Correction to resistance resolution section
    Explanation: previous calculations based on practical range of 25 mm. Actual practical range: 23 mm.
2023-01-14 Further analysis of battery life
    Added four citations to provide power usage data for all utilized components, allowing complete battery life analysis.
2023-01-19 Further clarification on analysis
    Added the specific P.I.D. constants specified by Pololu for the actuator we plan to use, as well as a few other minor changes. The analysis for stability and distance precision is in the two paragraphs above the abbreviation definitions section.
2023-01-22 Additions to battery life analysis
2023-01-23 Added constraint and analysis for "mountability"
    Added a constraint and analysis to describe the selected mounting hardware and justify it's use.
2023-01-25 Update benjaminreed-signoff-hdmiswitcher.md
    Updated hdmiswitcher to request a pre-built switcher to be purchased for analysis
2023-01-25 Added pressure range in analyis
2023-01-25 Specified reed switch as being for sensing speed in relevant constraint
2023-01-25 Update Mario Kart Rev 2 - Signoff - Mario Kart Bike Wireless Sensors Subsystem.md
2023-01-25 Mods to schematic, BOM, and content
    Implemented proof-of-concept schematic for how the button will function with a relay
    Fixed BOM to actually create a table
    Updated content to focus on using a relay to replace the button
2023-01-27 Update schematic
    Updated the schematic to include the GPIO pins for the Raspberry Pi. This also includes what pins are already taken, particularly for my own benefit.
2023-01-29 Updated camera constraints and analysis
    Added information for camera serial interface (data transmission protocol to be used), format, and data syncing.
2023-01-29 Changed board mounting solution
    Weight-bearing capability of new solution analyzed in second-to-last paragraph of analysis section.
2023-02-02 Updated schematic and design
2023-02-02 Update and rename Motor-stand.md to Linear-Actuator-And-stand.md
2023-02-04 Added HC-06 wireless transceiver to schematic
2023-02-04 Added socket for bluetooth tranceiver to BOM (for easy removal)
2023-02-06 Justfication of sensor appropriateness
2023-02-06 Updated schematic description and constraints
2023-02-06 Update schematic
2023-02-06 Fixed last commit's schematic
2023-02-09 Update PowerDistributionSystem.md
    Corrected constraints and analysis to be more concise and precise.
2023-02-09 Update PowerDistributionSystem.md
    Corrected Typo
2023-02-10 Update Linear-Actuator-And-stand.md
    Corrected constraints and analysis. Updated the subsystem model.
2023-02-10 Resistance resolution analysis revision
    Added more detail
2023-02-11 Analysis corrections
    Updated driving voltage constraint and analysis, removed distance precision from opening portion of resolution analysis
2023-02-11 Analyzed actuator duty cycle by citing Arduino PID library function
2023-02-11 Minor inequality correction
    On wireless communication analysis section
2023-02-11 Corrections and addition to BOM
    Supplier numbers were part numbers, part names not specific enough; added two socket headers for easy connection and disconnection of Arduino.
2023-02-12 Update PowerDistributionSystem.md
    Update Drawing and Made Larger. Updated analysis and over protection devices.
2023-02-13 Update to BOM
2023-02-13 Update to resistance state constraint analysis
2023-02-14 Update PowerDistributionSystem.md
    Updated Drawing: Replaced fuses with 3 Amp circuit breakers and labeled correctly with amperage rating. 3.15 A slow blow is generic recommended by the manufacturer covering multiple sized power supplies. I would normally go up to the next size, but 4 A would allow for too much power. I would be more comfortable at 3 Amps.
    Updated A3. Over protection rating
    Updated A5. Means of De-Energizing
2023-02-15 Revision to address states constraint
    After analysis of the resistance states, it was determined that the current resolution was insufficient to handle the smallest changes in distance corresponding to state changes as defined in tables 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
2023-02-15 Revision to add ADC
    [Actuator Driver-B_Cu.gbr, Actuator Driver-B_Mask.gbr, Actuator Driver-B_Paste.gbr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]
2023-02-20 Revision to condense constraints and analysis
    Applied feedback previously given on actuator controller subsystem signoff to this signoff with help from Ray Durlin.
2023-04-16 Accidentlly put these in the wrong spot
    [rec_led.py, rrsa.py, speed.py]
2023-04-29 RRSA model
    Please note that the .stl model files exceed the 25 MB github.com upload limit; therefore it is impossible for me to upload them.
2023-05-01 Add rumble data research spreadsheet
    Added spreadsheet with data used to write rumble_data.md.
    [rumble_research.xlsx]
